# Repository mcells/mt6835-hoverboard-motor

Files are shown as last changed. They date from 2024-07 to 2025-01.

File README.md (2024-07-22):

# mt6835-hoverboard-motor
MT6835 Breakout board, eg. for mounting inside Hoverboard motors

| Front | Back |
| ----- | ---- |
| Top side | Top side |

## Features
- MT6835 Encoder
- 25x25mm diagonal M3 mounting holes that are removable by breakaway sections
- 14.2mm diameter, making it small enough to fit onto the 15mm shaft of Hoverboard motors
- M2 mounting holes, 10.6mm apart to facilitate mounting.
  - Nonconductive screws or spacers are necessary to prevent shorts!
  - Designed to be screwed into corresponding M2 holes drilled and tapped into the shaft, the cabling will go through the drilled-out center of the shaft.
  - A similar approach is described [here](https://community.simplefoc.com/t/a-project-in-mind-force-feedback-wheel/952/27)
- Breakaway drill template
  - drill out the motor shaft to 5mm and use the drill bit to locate the template on-center, then mark and drill the M2 holes
- All usable Pins broken out to three sensible 6-pin headers
  - SPI interface on 1.27mm header, with enough space to mount a 6-pin 1.25mm Molex Picoblade
  - UVW and ABZ (together with CAL and PWM pins) on 1mm Pitch headers (due to space constraints)
- TVS diode footprint can accept the one from the breakout board commonly available on Aliexpress
- Sleek design
## Renders
| Front | Back |
| ----- | ---- |
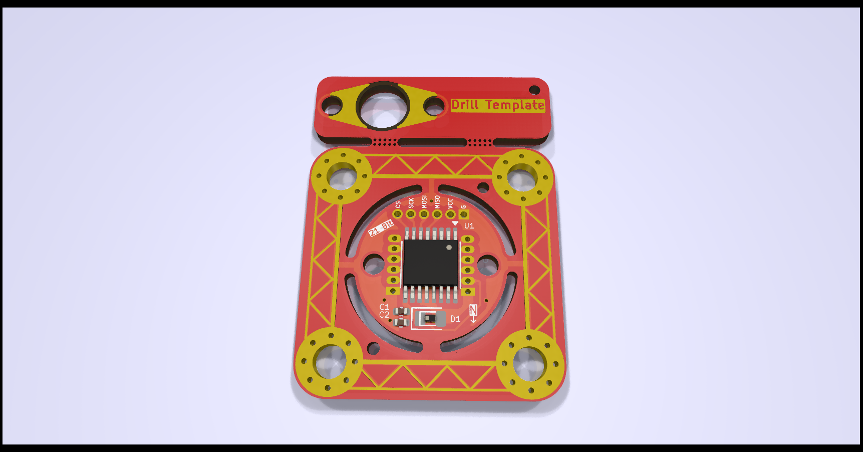
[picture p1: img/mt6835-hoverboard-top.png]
Top side
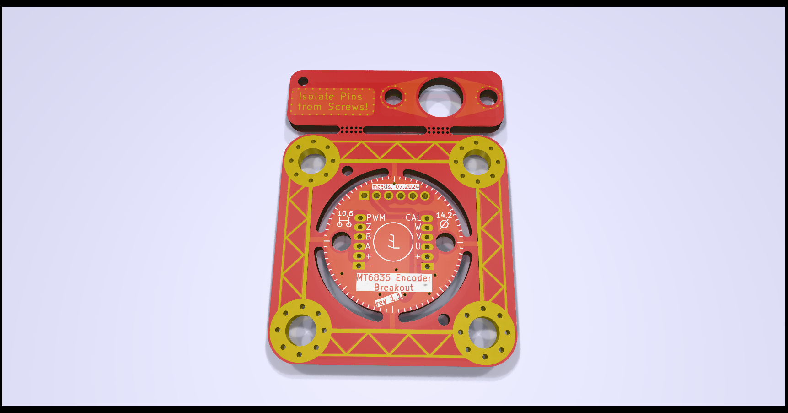
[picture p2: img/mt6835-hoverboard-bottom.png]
Bottom side
|  |  |

## Installation inside a Hoverboard motor

Installing the sensor board inside a Hoverboard motor requires you to have access to the following tools:
- A Hoverboard motor and
- A sensor board (obviously...)
- A drill press (though using a hand drill might work, if you are careful)
- 5mm HSS drill
- 2mm HSS drill for marking the locating holes
- 1,6mm or 1,7mm HSS drill for the M2 threads
- M2 tap
- two M2 screws for mounting the sensor
- soldering stuff
- a saw or dremel to cut out the round part of the PCB

### Steps

| Step | Image | Description |
| ---- | ----- | --- |
| 1  | | Disassemble the Motor, until you have just the bare Stator. Desolder and pull out all wires, so you can drill through the shaft.|
| 2  | Step 2 | Drill a 5mm Hole inside the top of the stator shaft. There is a centered "dimple" already in the shaft, which helps with centering the drill enormously. You want everything to be as concentric as possible, else you will get a periodic nonlinearity in the measured angle! You have to drill about 25mm until you break through to the hollow shaft. |
| 3  | Step 3 | Remove the drill bit from the drill and put it most of the way through the new hole, so that just protrudes at the top. Use the drill bit to locate the template PCB on the center of the shaft. | 
| 4  | Step 4 | Either use a center punch, or, using a M2 drill bit, pre drill two "dimples", so you can later locate with the smaller drill bit. When drilling the second dimple, use something like a small allen wrench in the first dimple to hold the template in place. |
| 5  | Step 5 | Drill the two holes with a 1.6mm or 1.7mm bit and tap the holes to M2. You can use a 1.7mm drill to ease the tapping, as the threads don´t need to support any significant load. Also refrain from tapping more than a few mm deep, as it is absolutely not neccesary and just increases the risk of your tap snapping off. |
| 6  | Step 6 | You can now mount the sensor. Take care to use either 3d printed isolators like I did, or use plastic washers. Else you **will short** the sensor out! I had to drill out the 5mm hole to 6mm to make my sensor wires fit. If you have thinner wires, 5mm might be enough for you. I replaced the original wiring with new one. |
|  7 (optional) | Step 7 | In these motors, the 3 phases are each wound using multiple strands of enamelled copper wire, some 3, 4, or even 5 in parallel. The phases are then connected in a star, or Y topology. I wanted to lower the kV as much as possible, so I unsoldered the strands and connected them in series for each of the three phases. This lowers the kV by the number of strands you serialize, in my case three. |
|  8 | Step 8  |  My motors have just enough space inside, so that the magnet can be mounted directly inside the rotor bell. I marked the center of the bell by pushing a 15mm HSS drill into the bearing (15mm inside diameter) and turning the bell. This leaves a perfectly centered dimple exactly where you want to mount the magnet. The aluminium there is about 2-3mm thick. Drilling about 1mm with a drill bit of the same diameter as your magnet lets you just glue the magnet there, without drilling from the outside. |

## Where to get the boards

I got my PCBs fabbed and assembled at JLC. You can use the provided KiCad project files to generate the required files.
You don´t have to get assembled boards directly, as I designed the PCBs so that you can desolder the components from the aliexpress board and solder them onto this PCB. This might be far cheaper for single quantities.

If you have any questions, feel free to just create an issue/discussion or ask me on Discord (@hollowedbethyname)

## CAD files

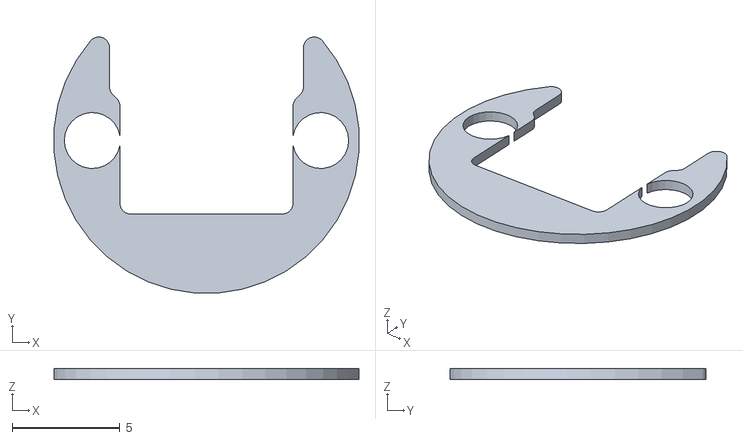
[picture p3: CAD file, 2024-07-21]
3d-prints/Isolator-top.stl
14.2 x 11.9 x 0.5

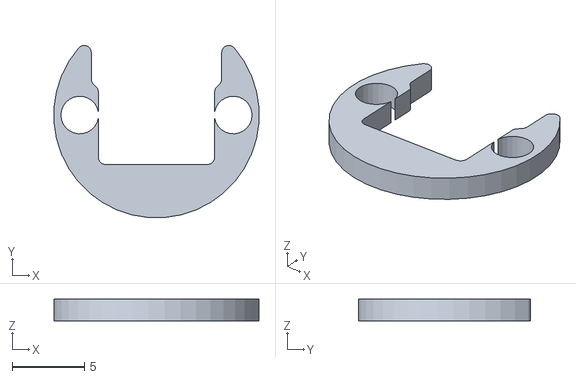
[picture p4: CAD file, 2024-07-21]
3d-prints/isolator-bottom.stl
14.2 x 11.9 x 1.50

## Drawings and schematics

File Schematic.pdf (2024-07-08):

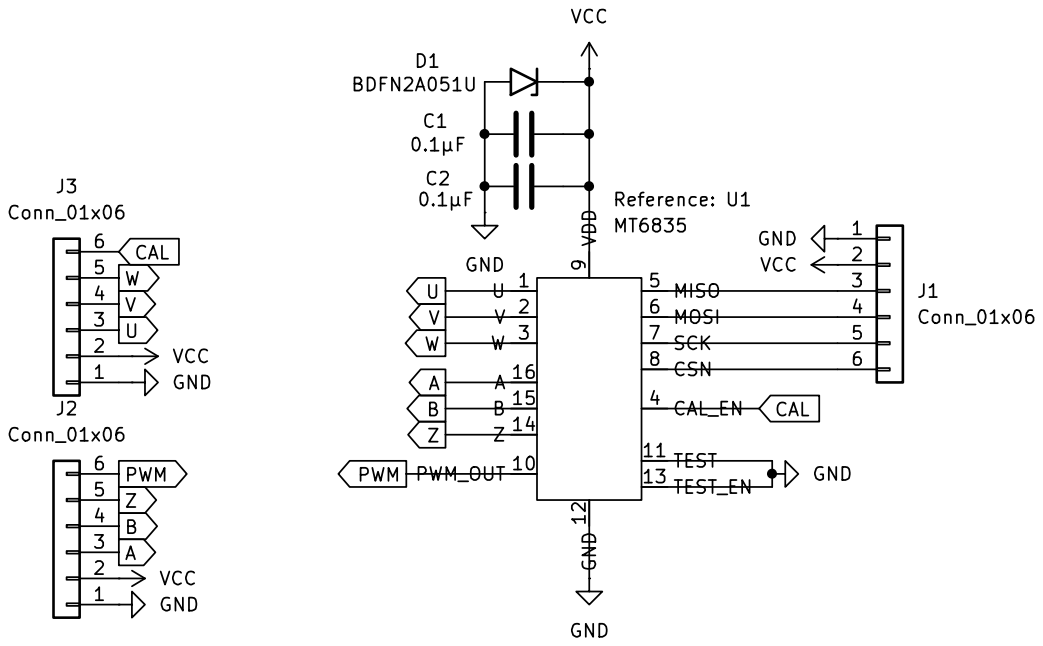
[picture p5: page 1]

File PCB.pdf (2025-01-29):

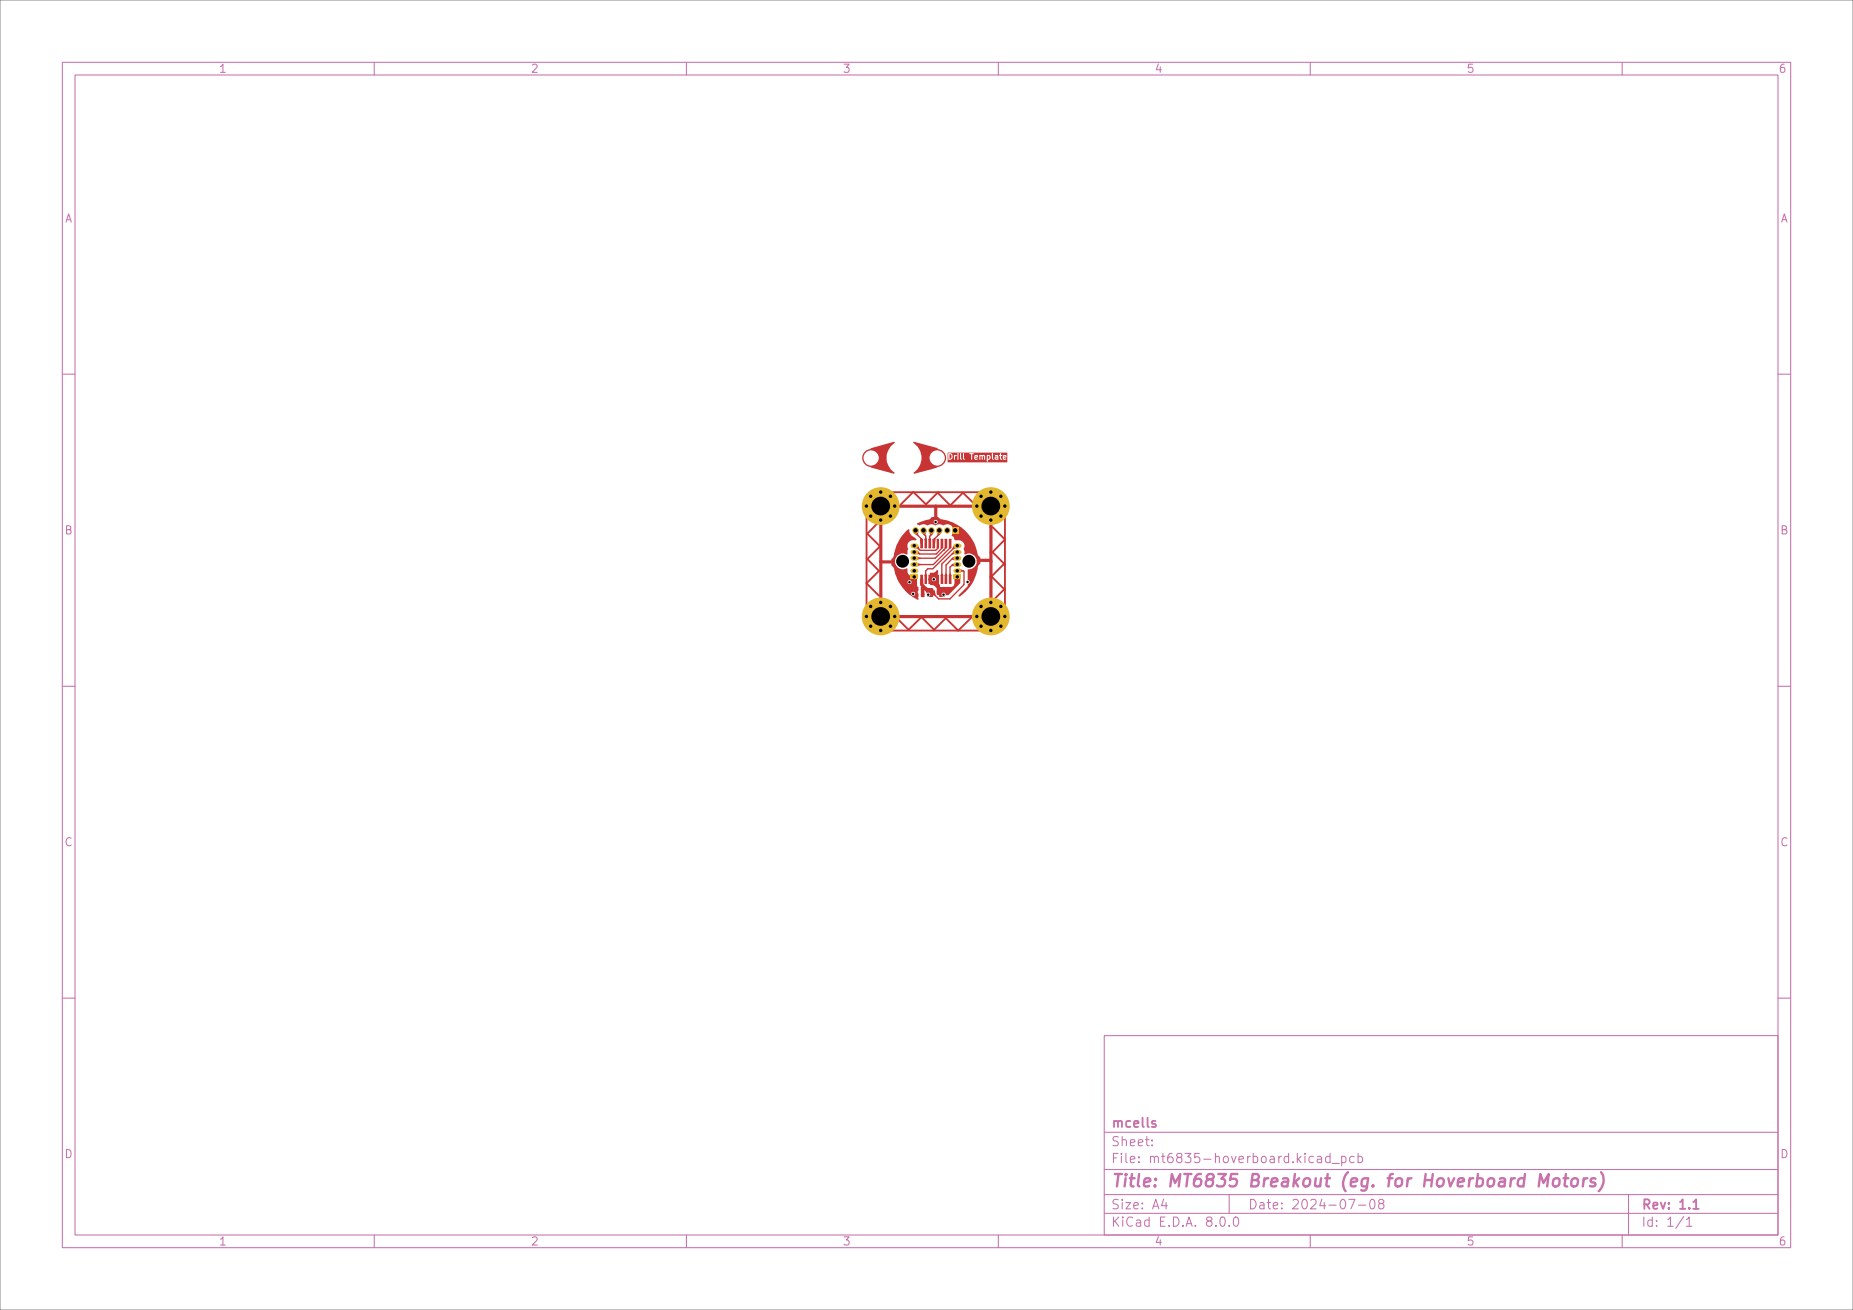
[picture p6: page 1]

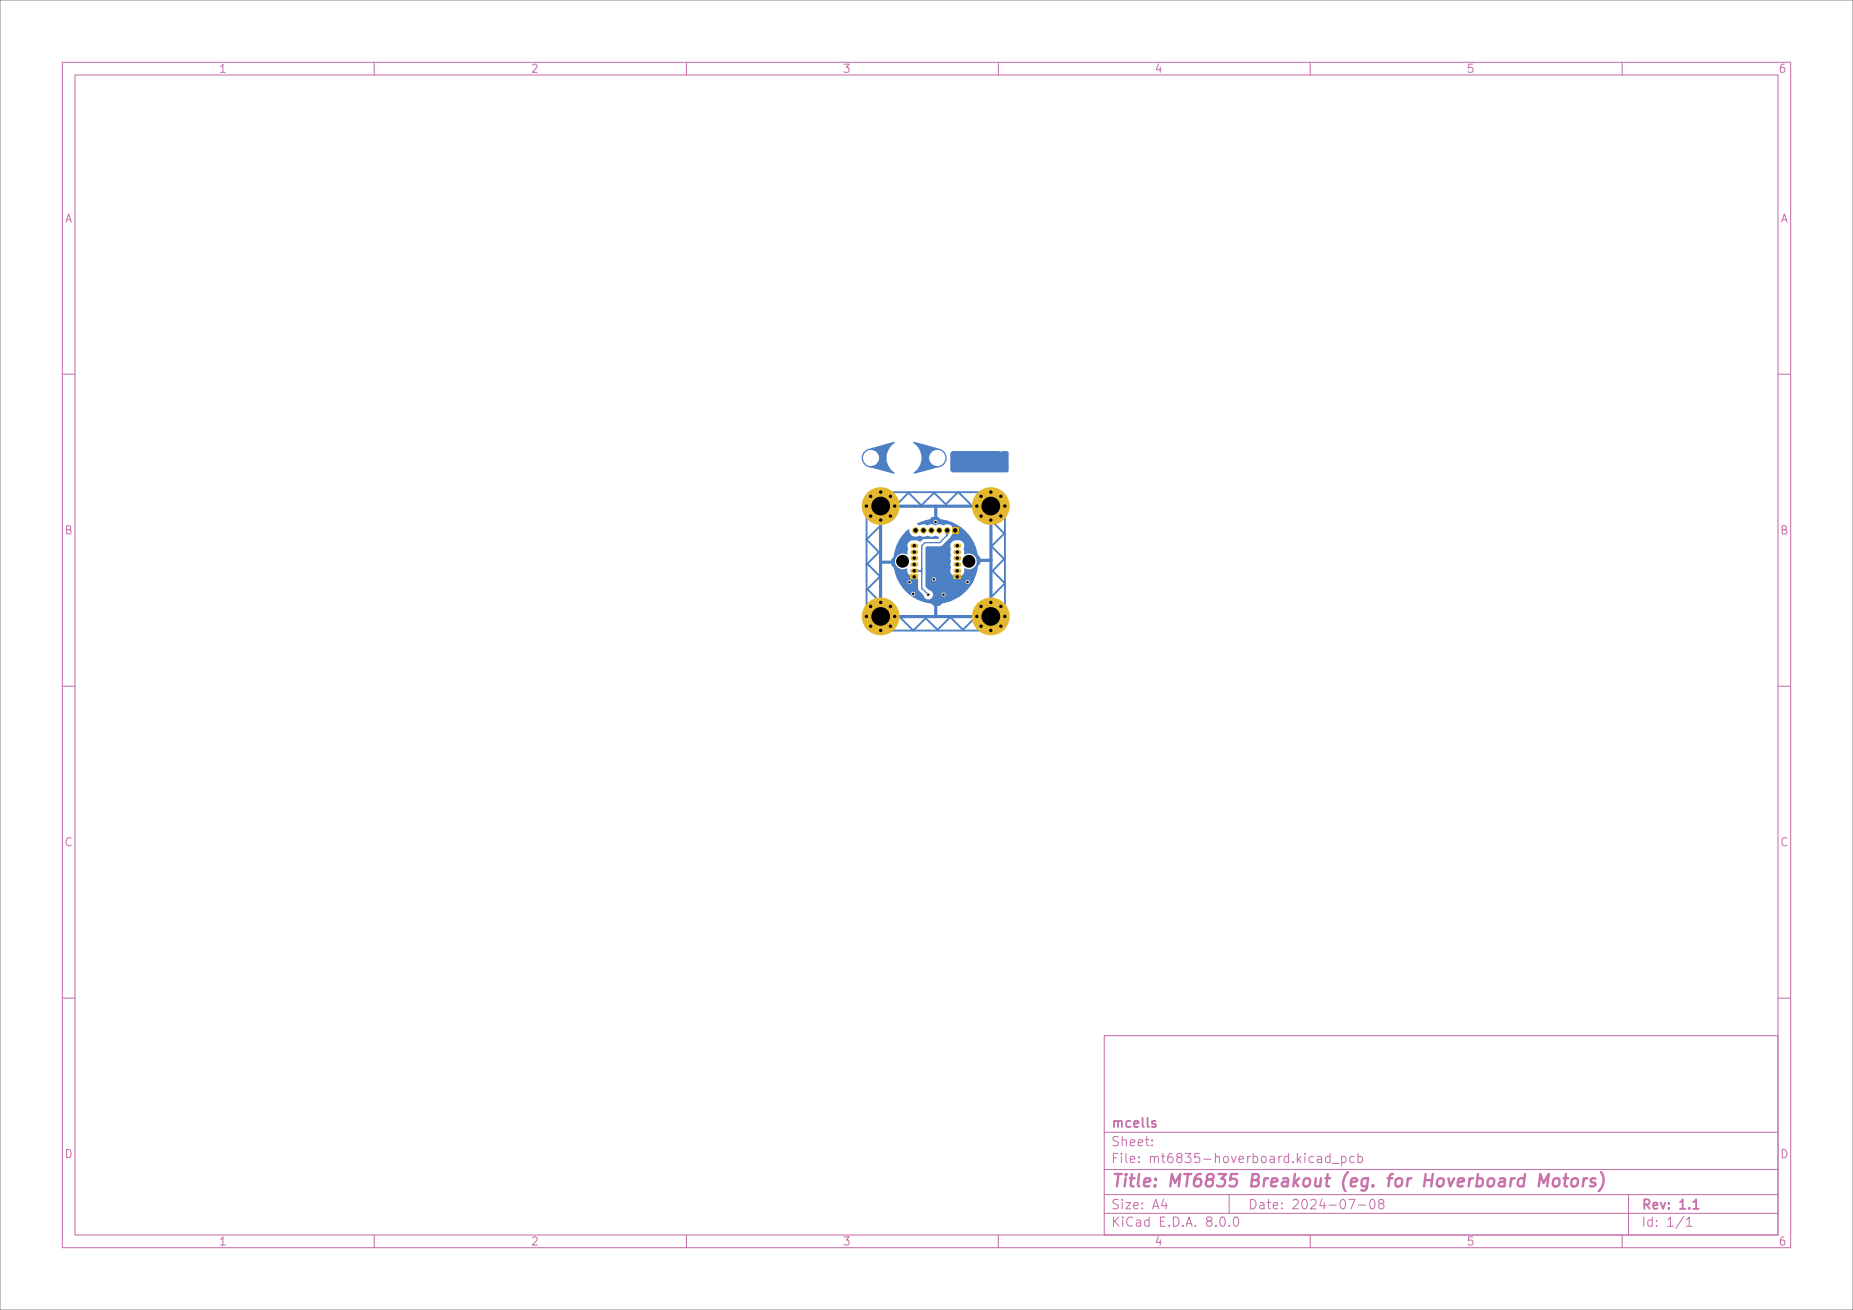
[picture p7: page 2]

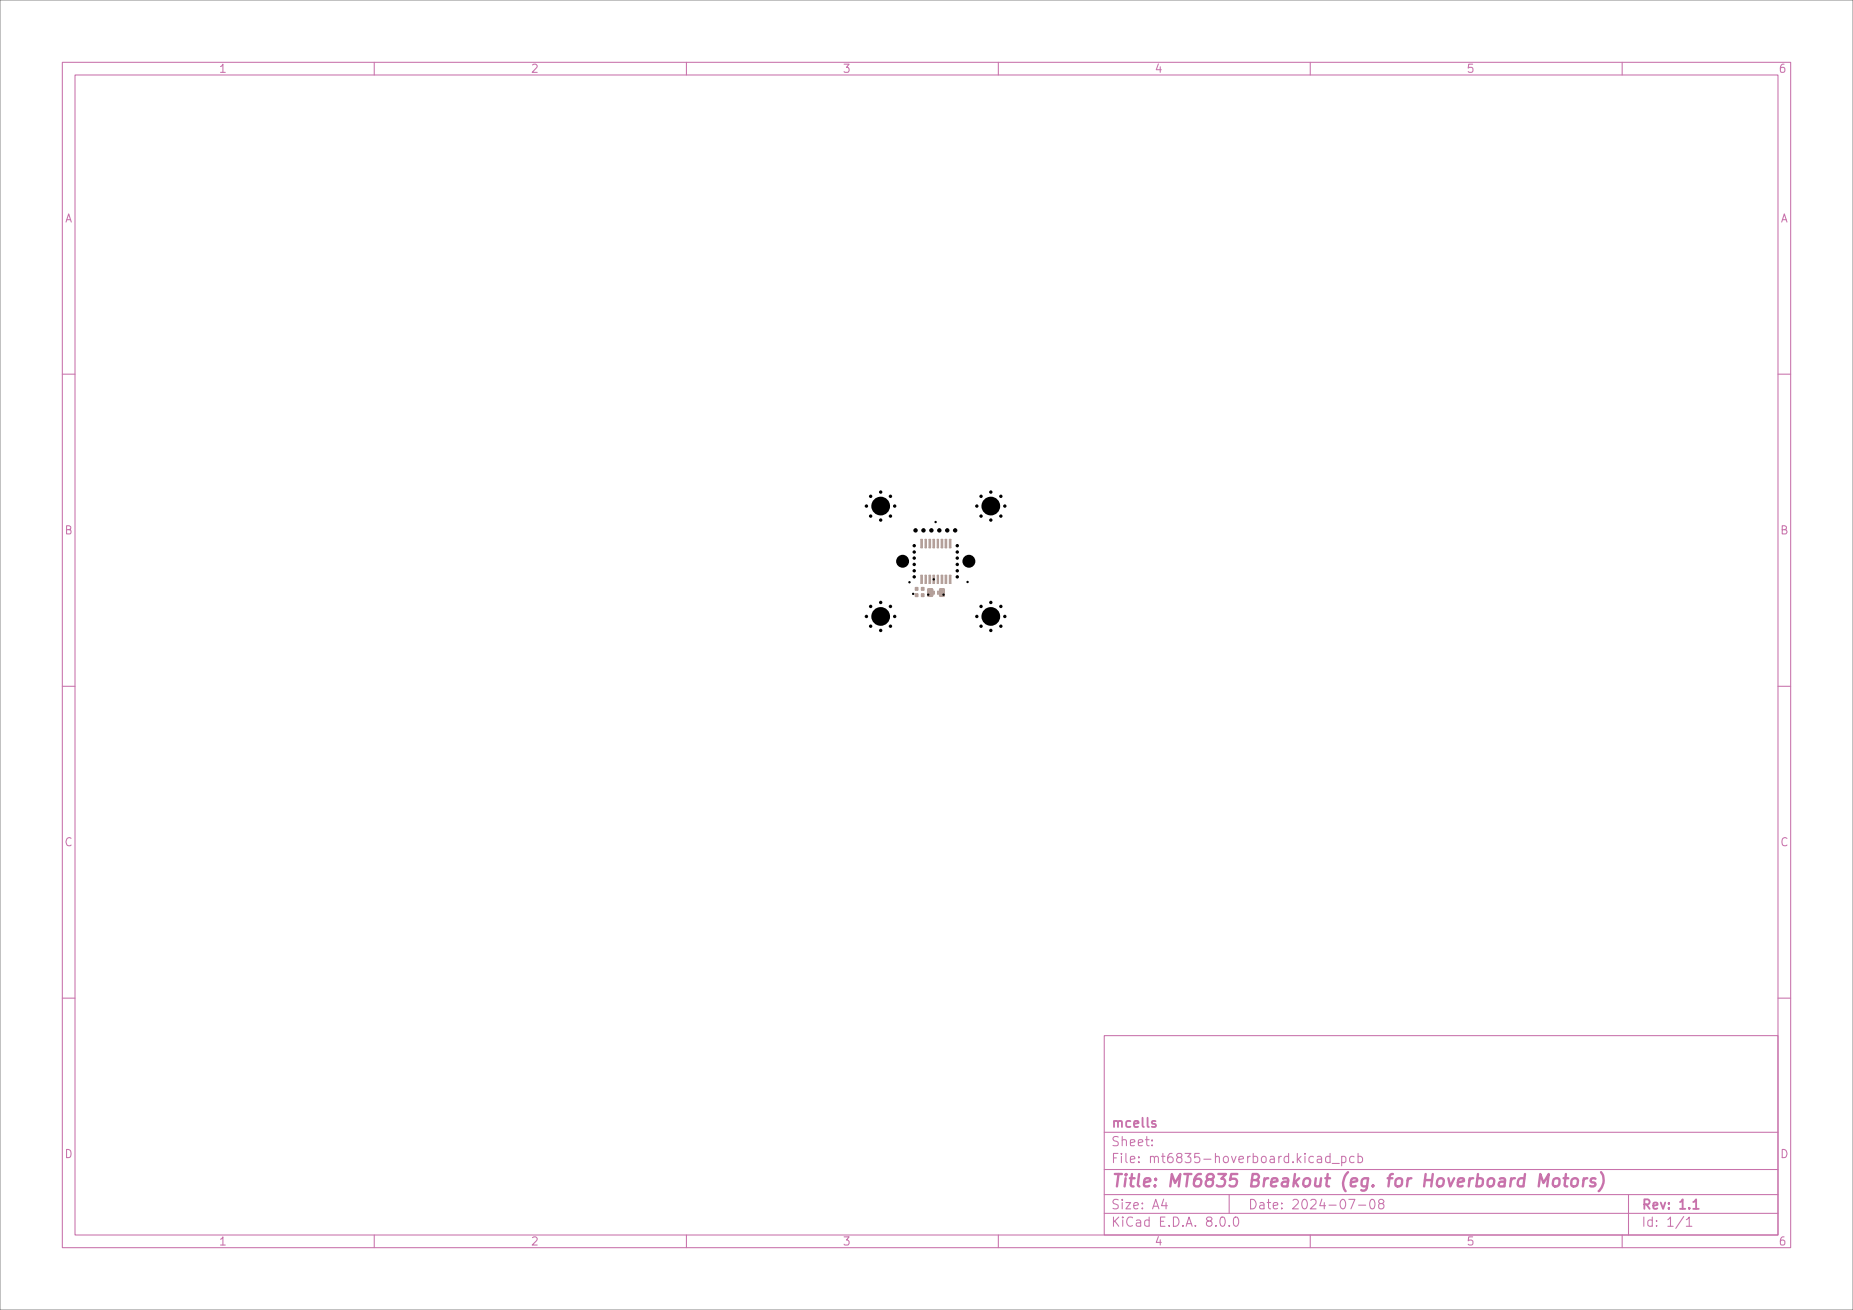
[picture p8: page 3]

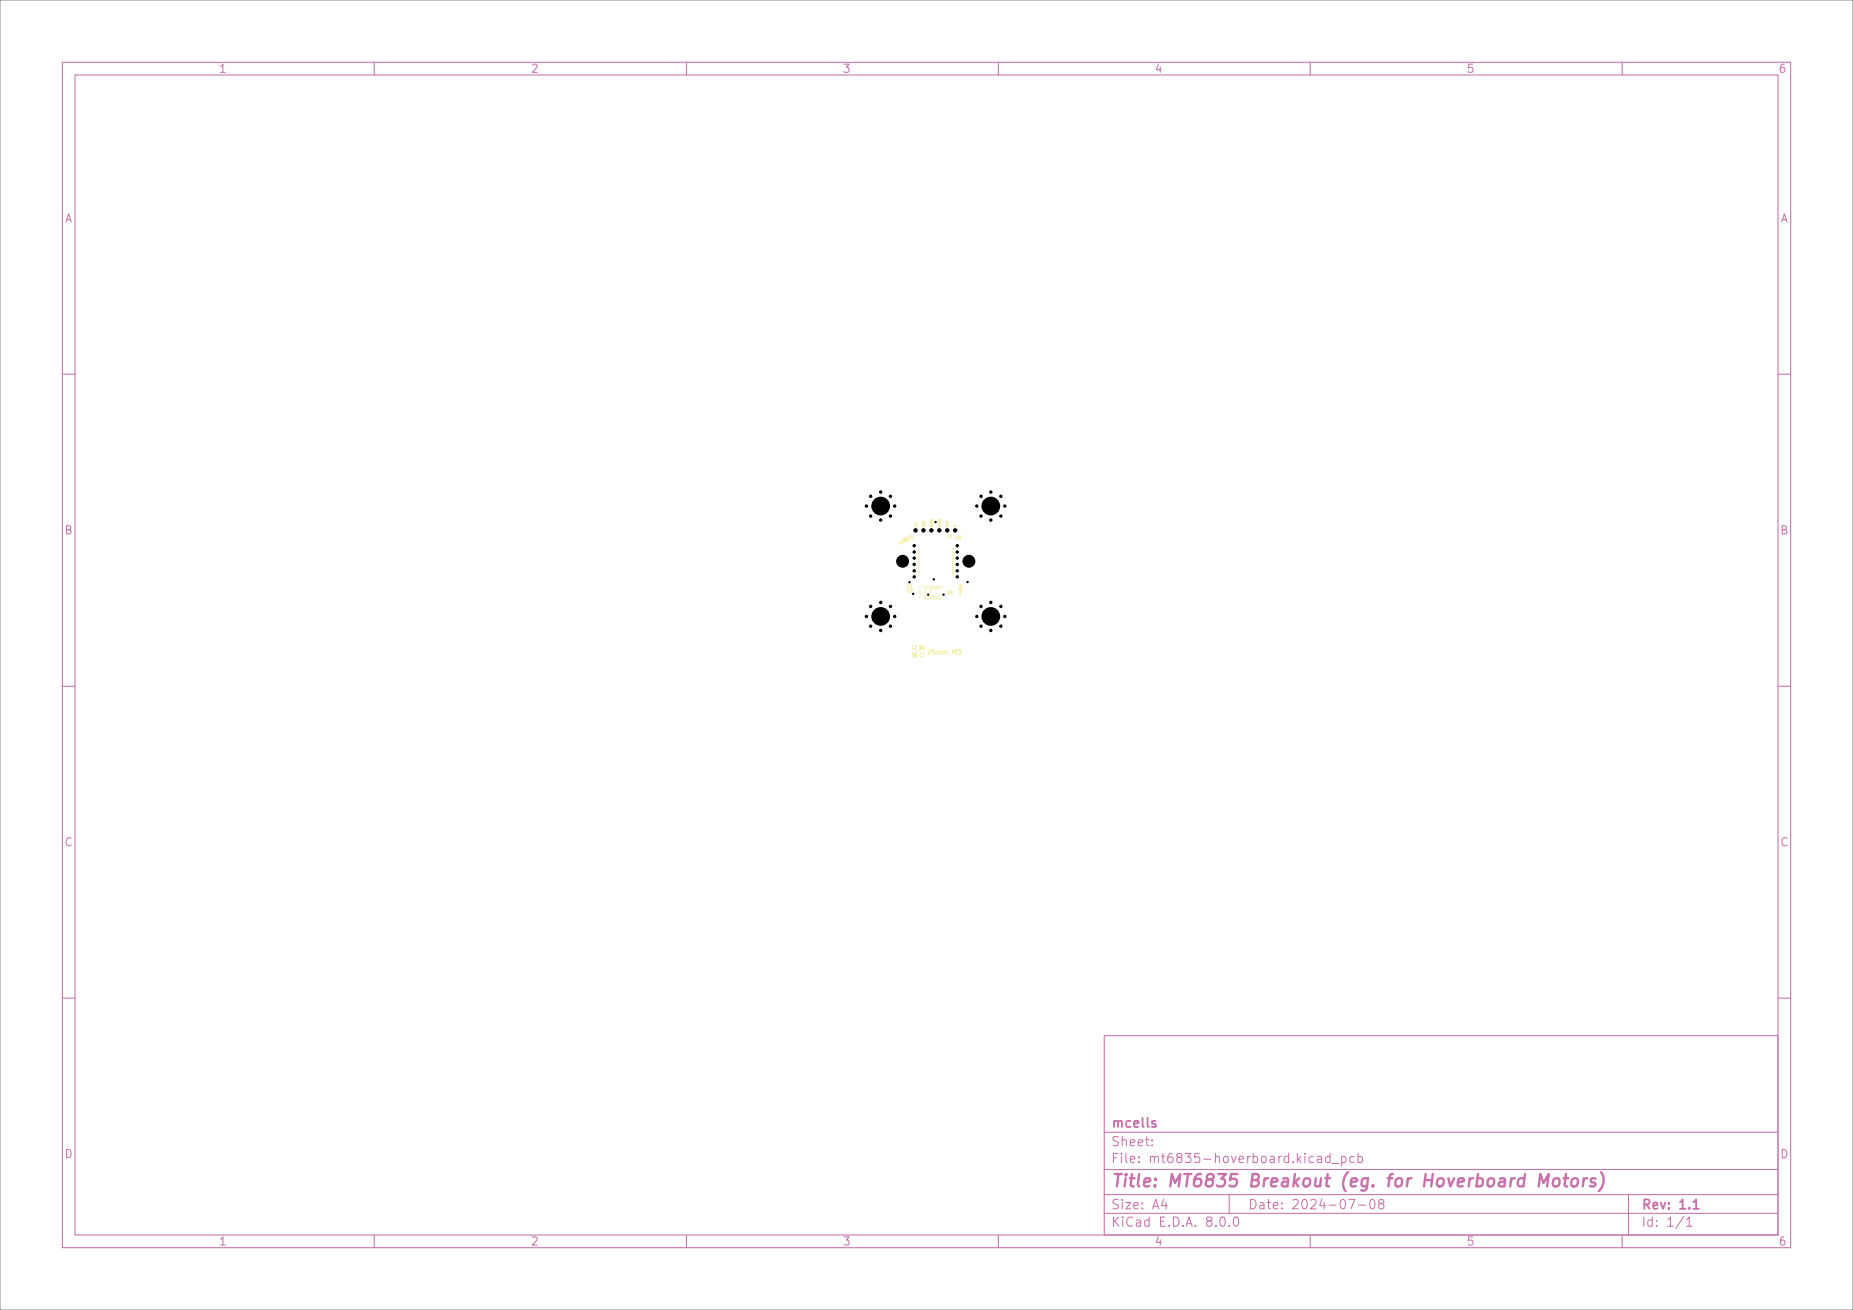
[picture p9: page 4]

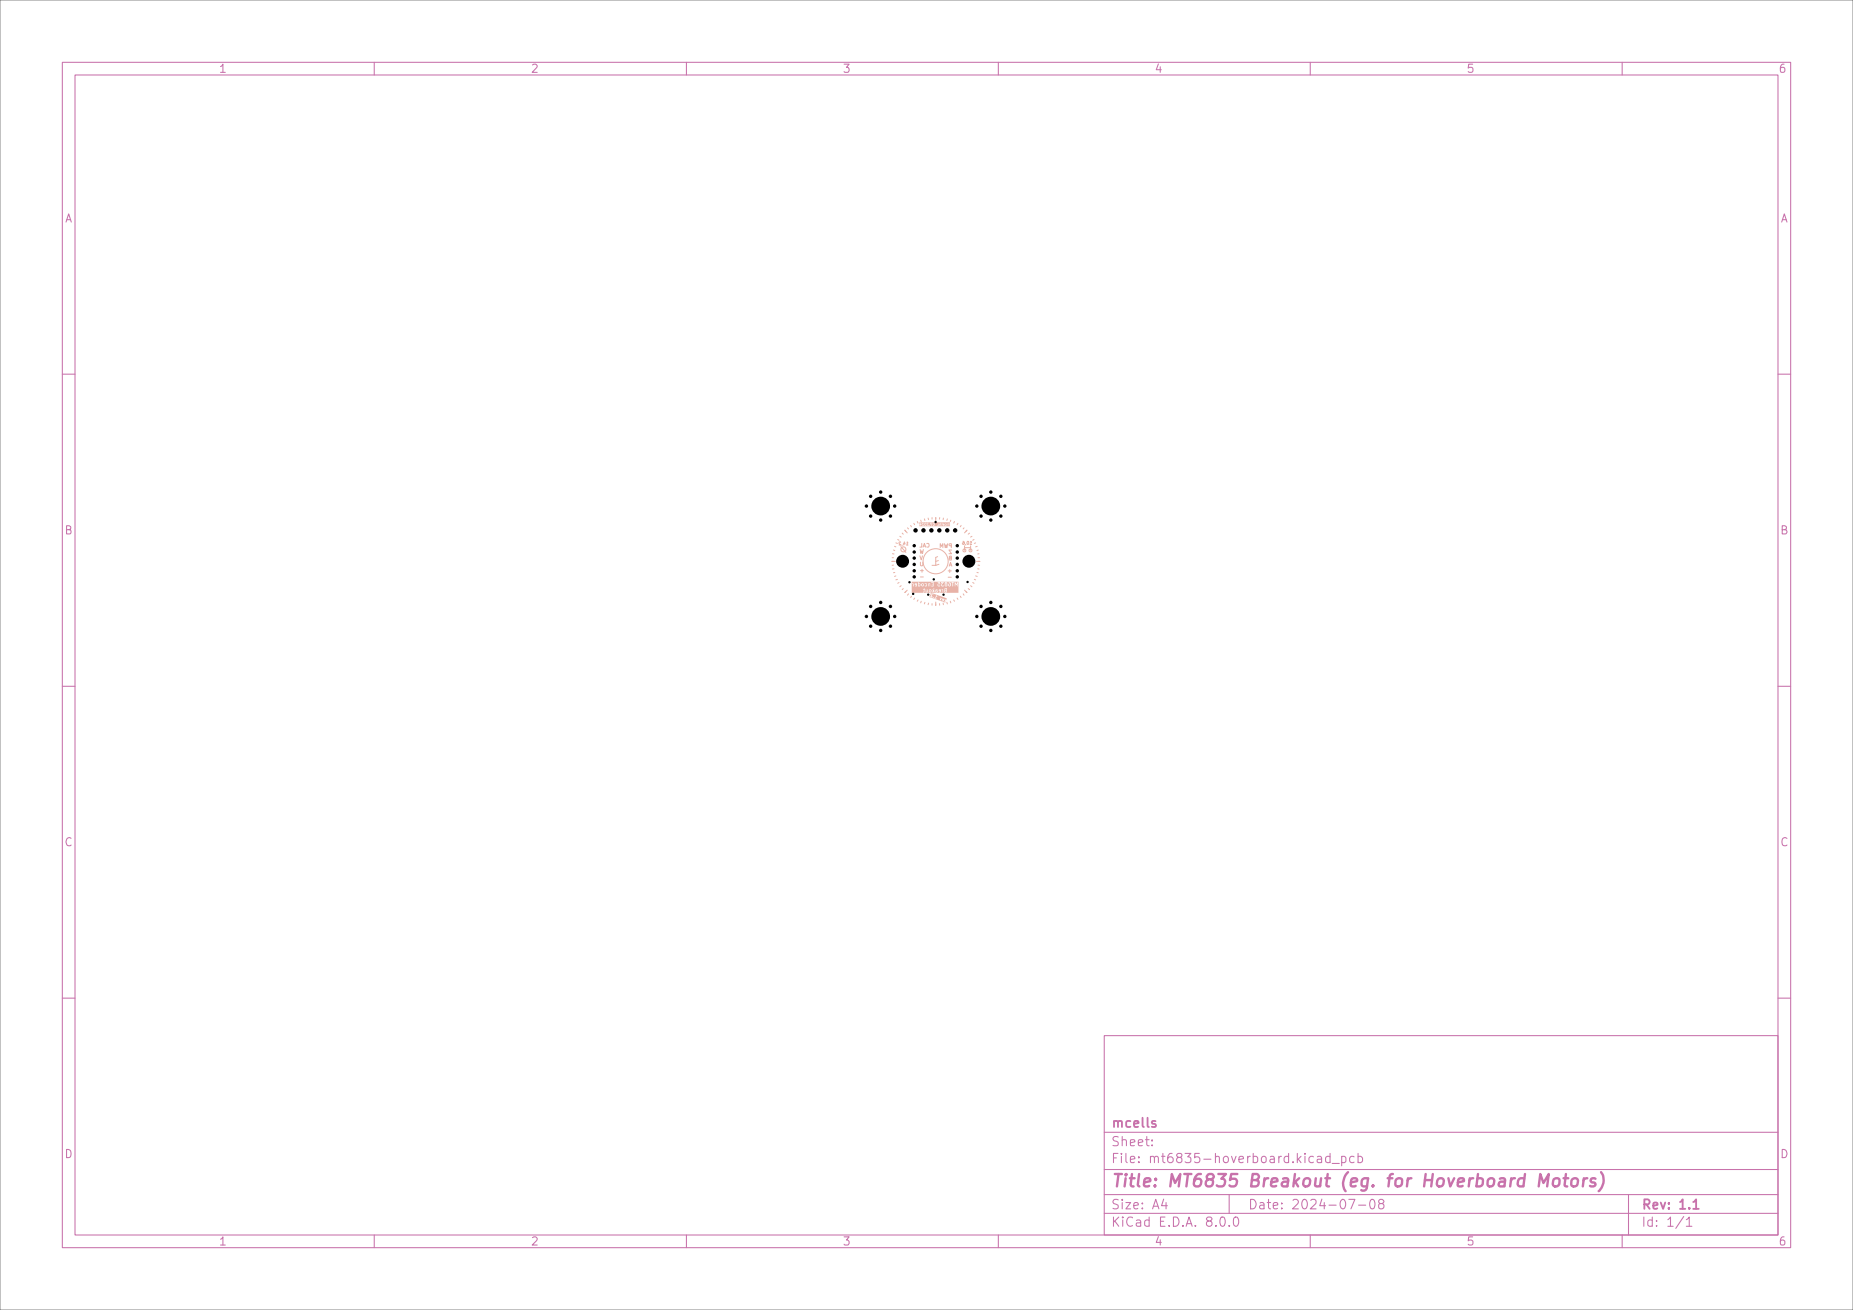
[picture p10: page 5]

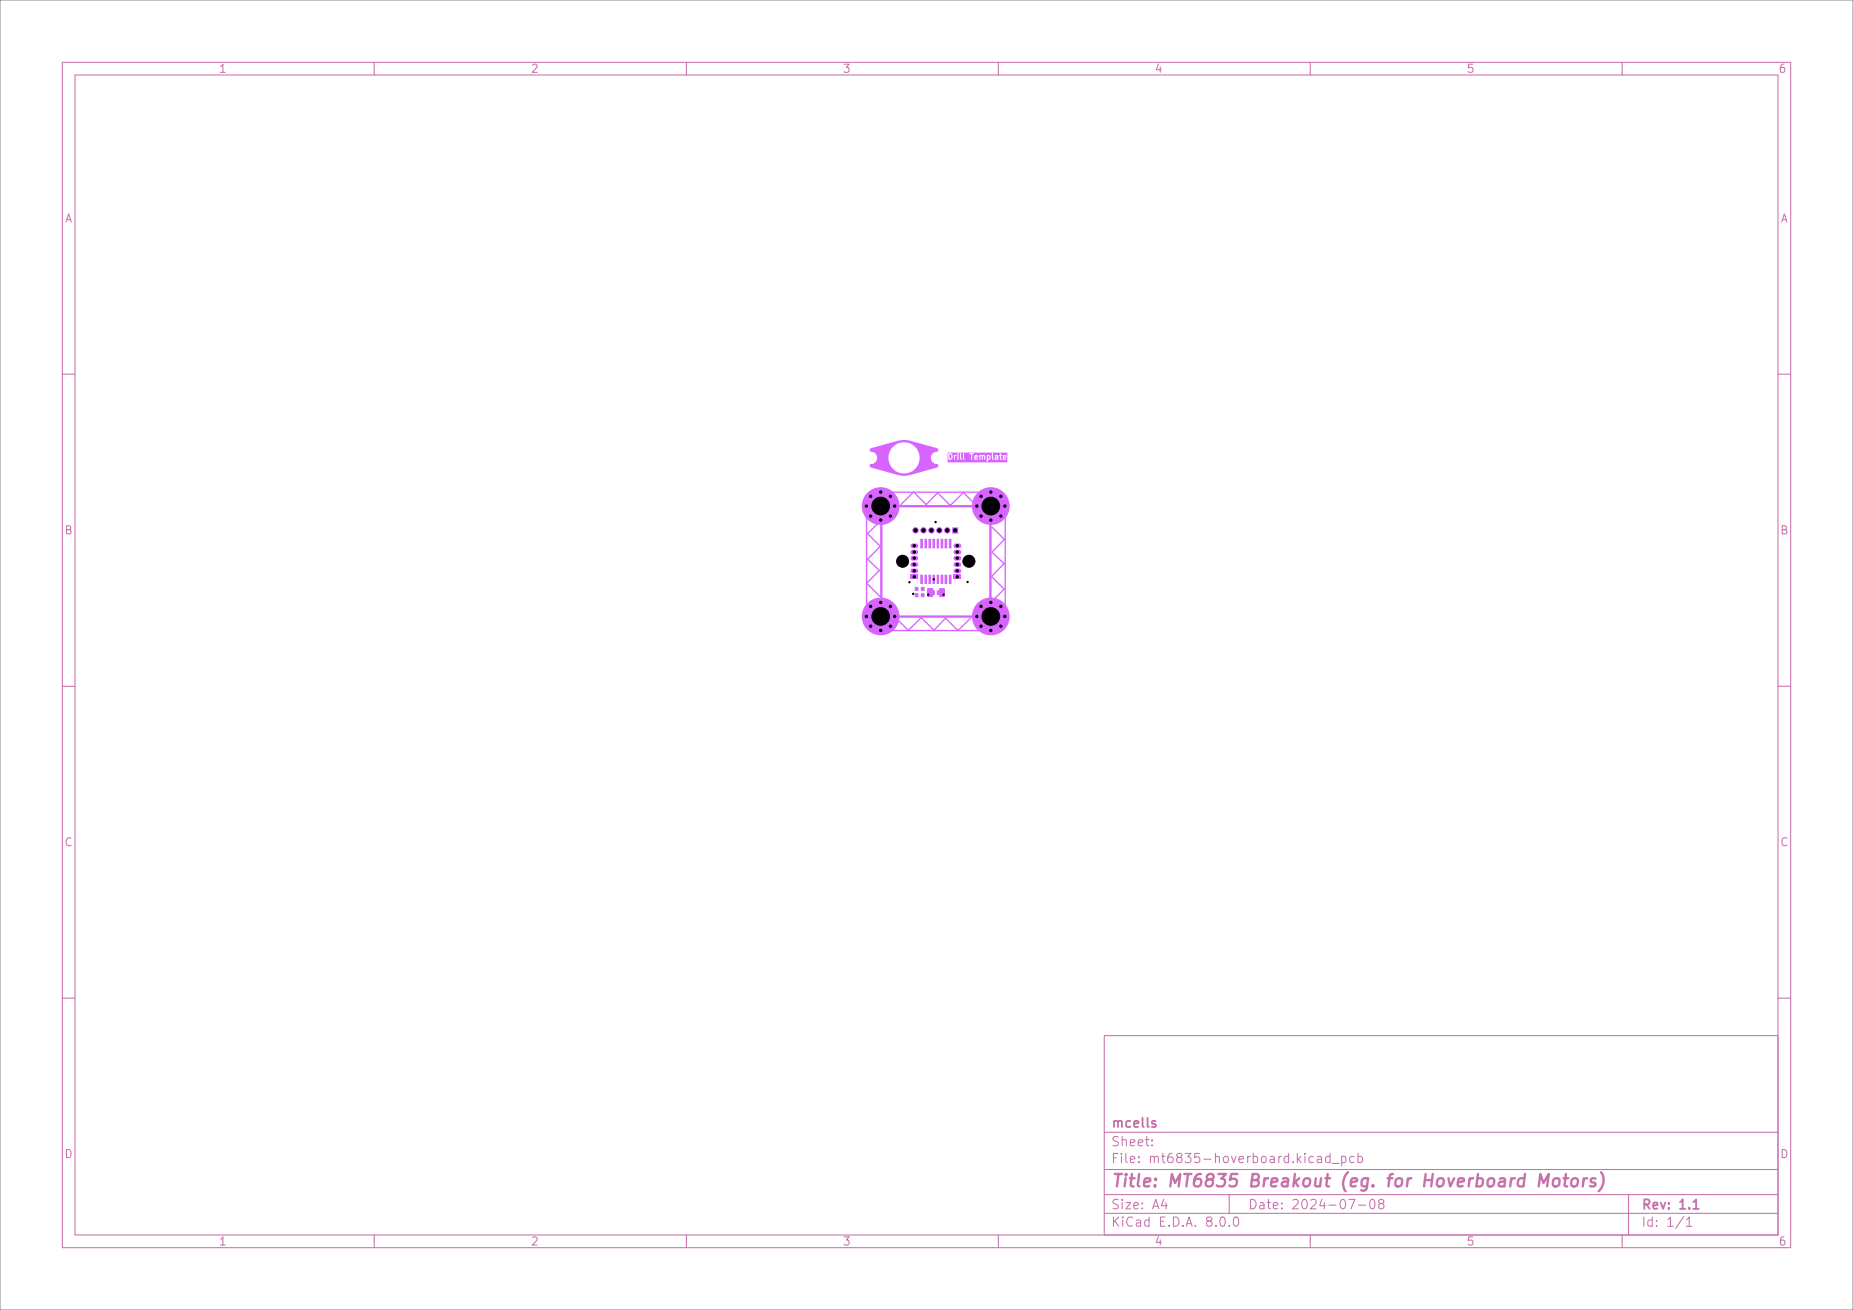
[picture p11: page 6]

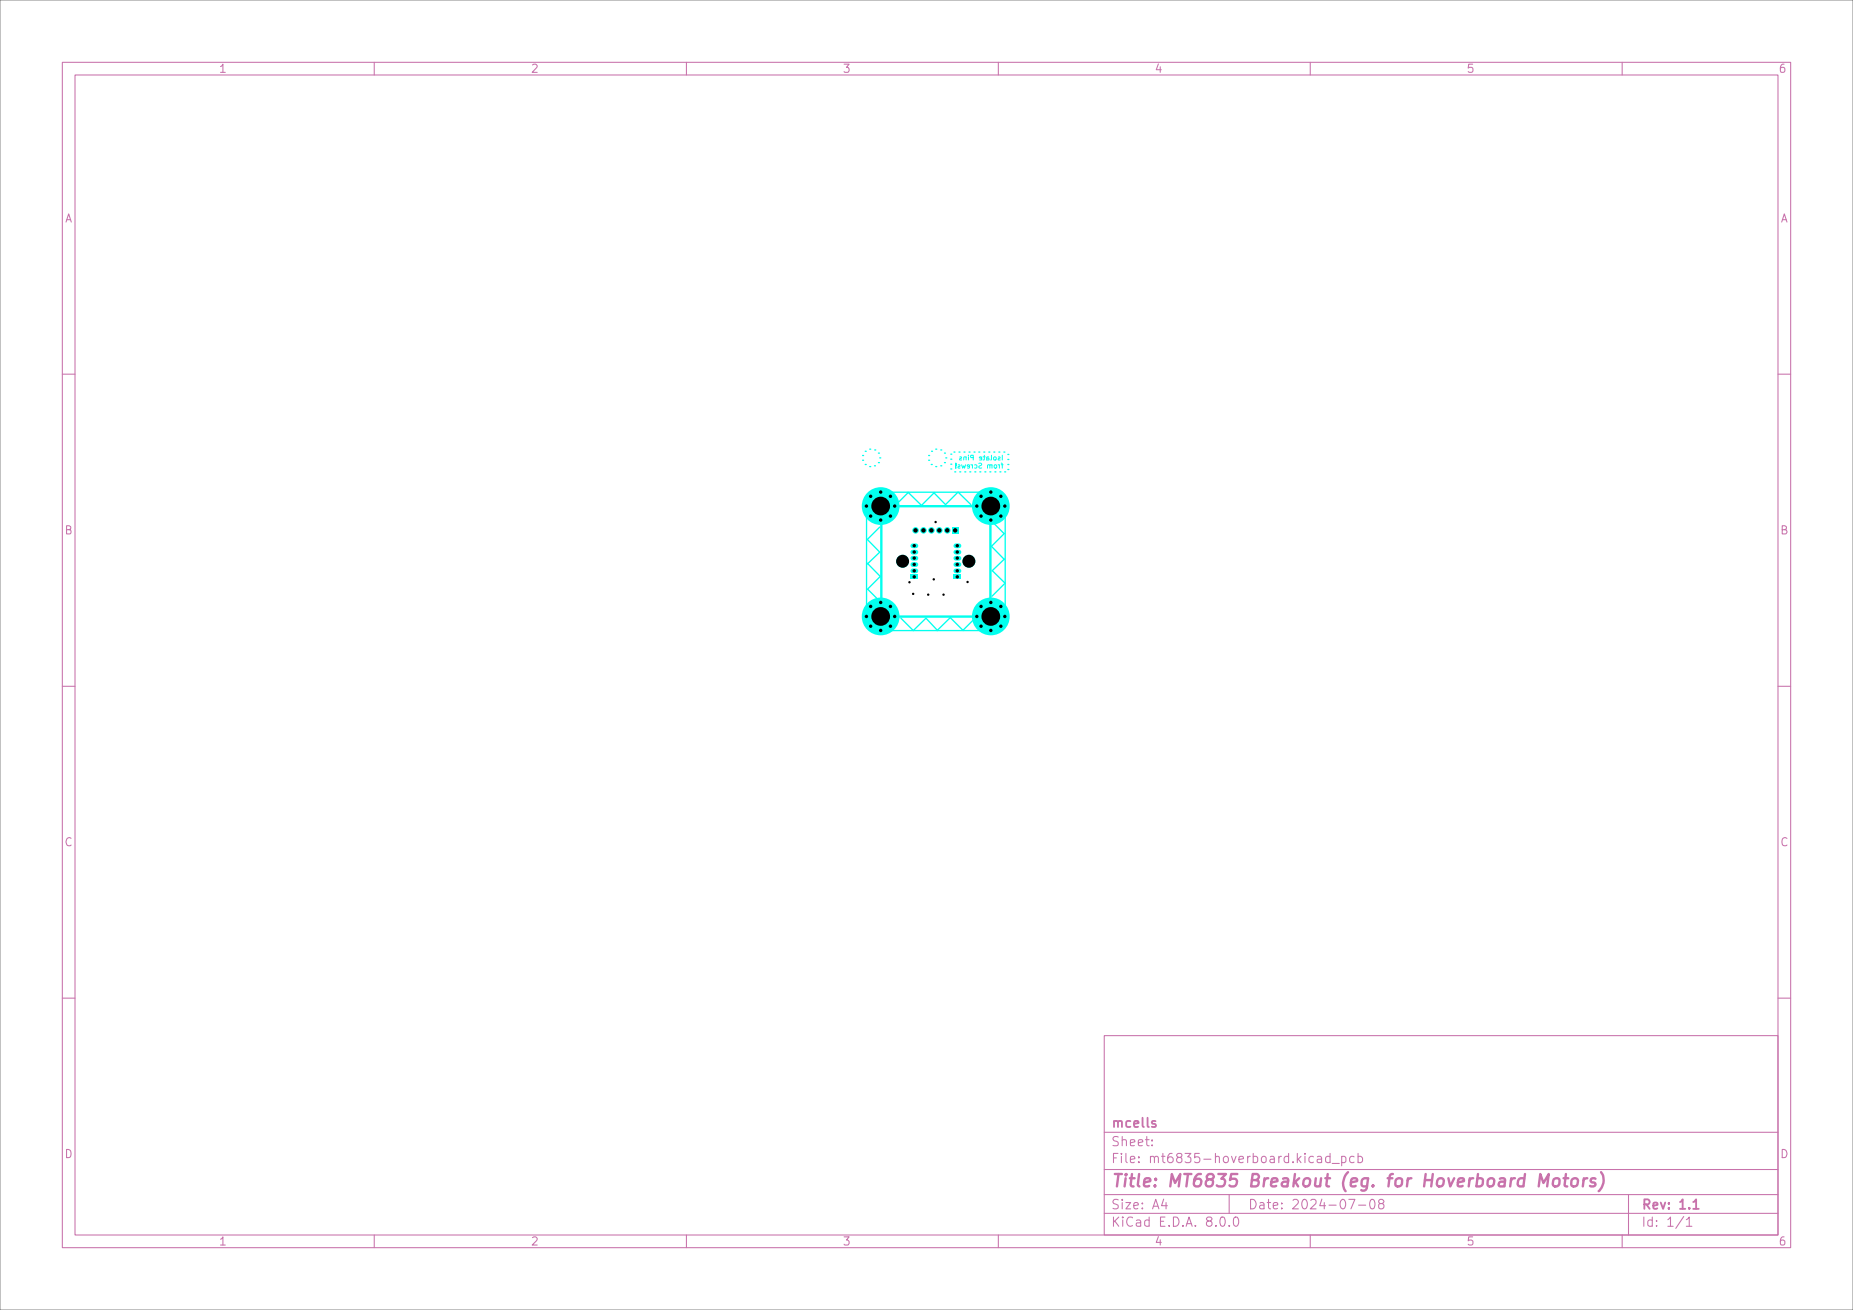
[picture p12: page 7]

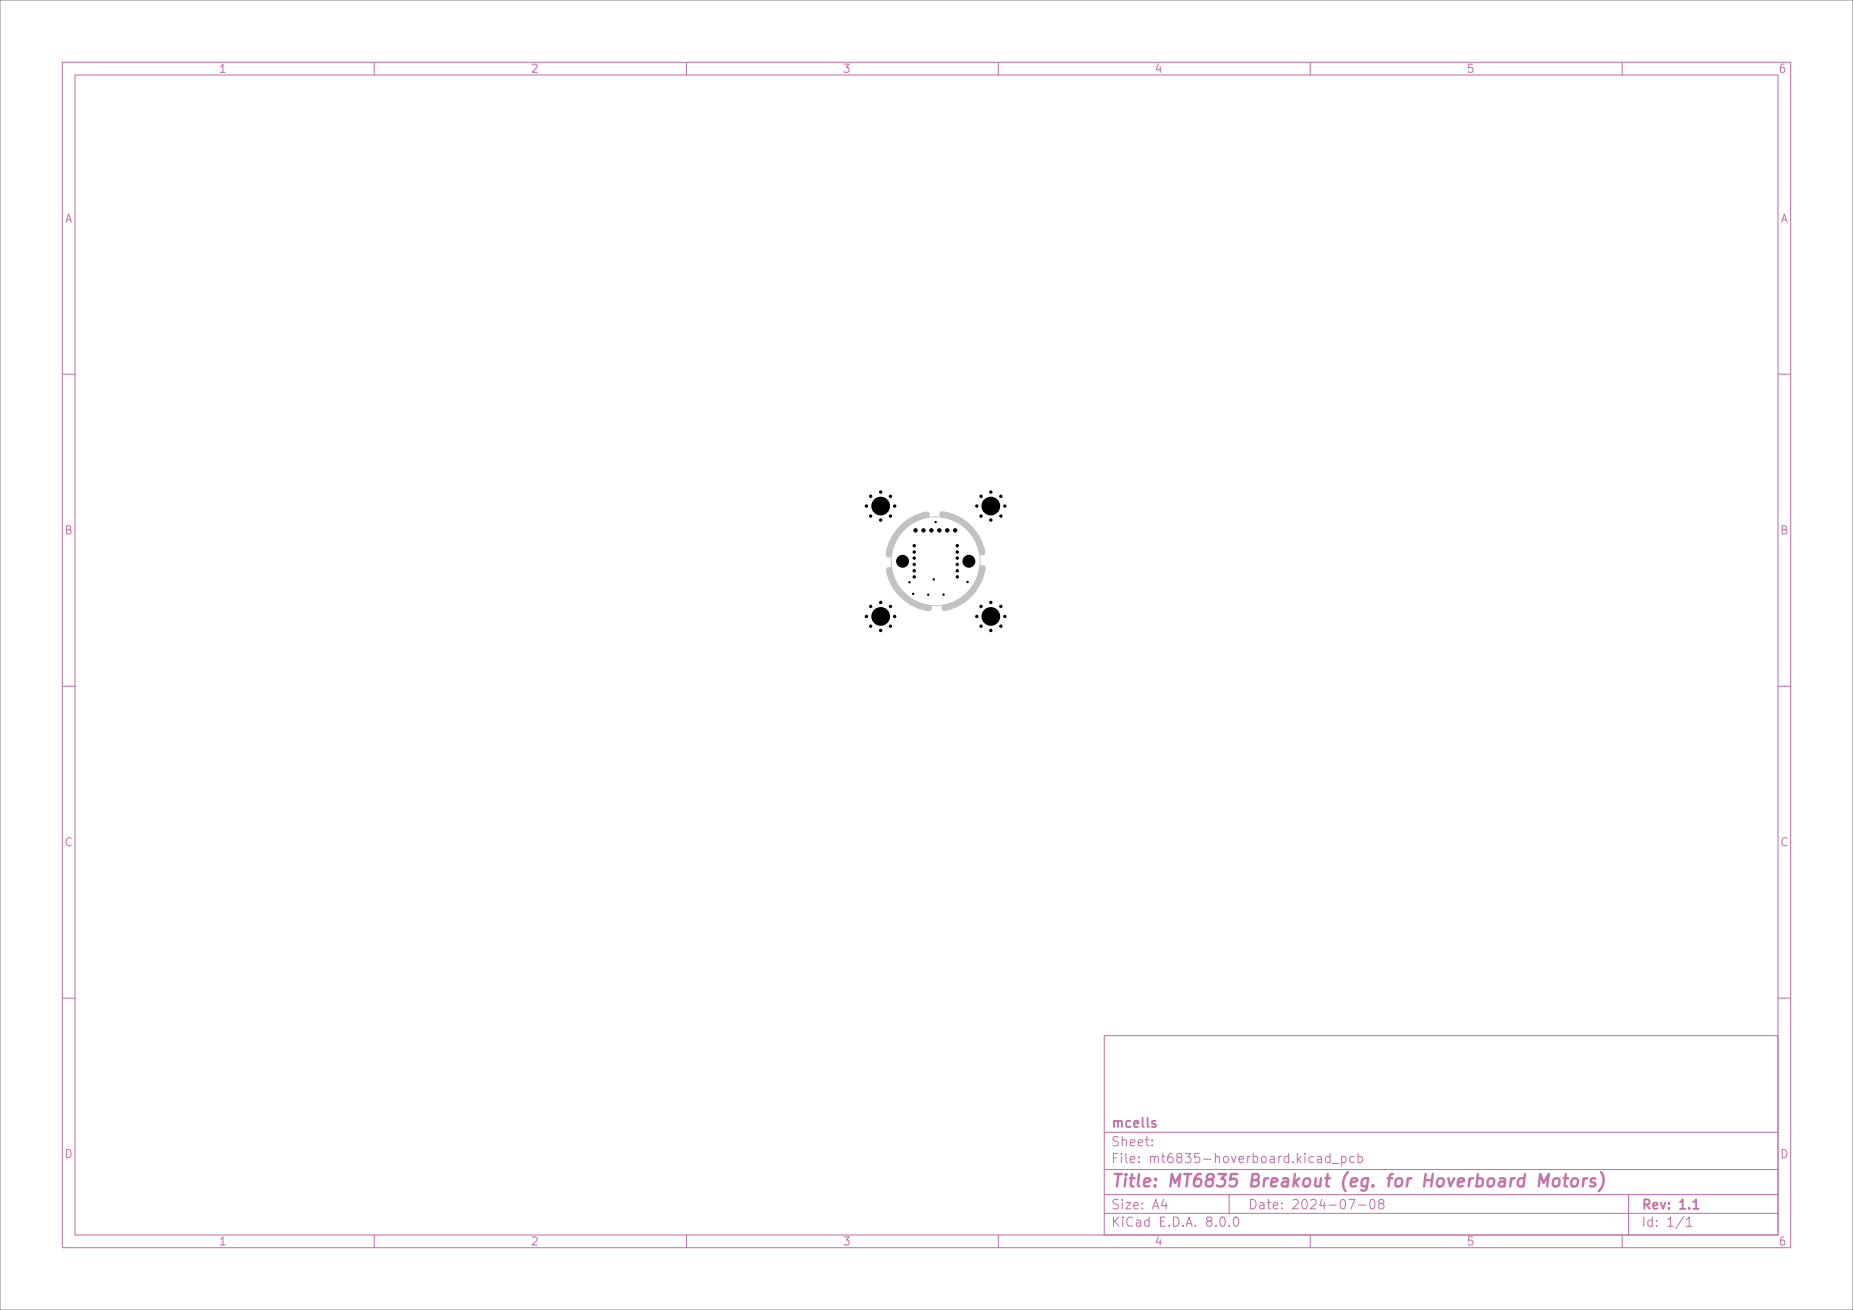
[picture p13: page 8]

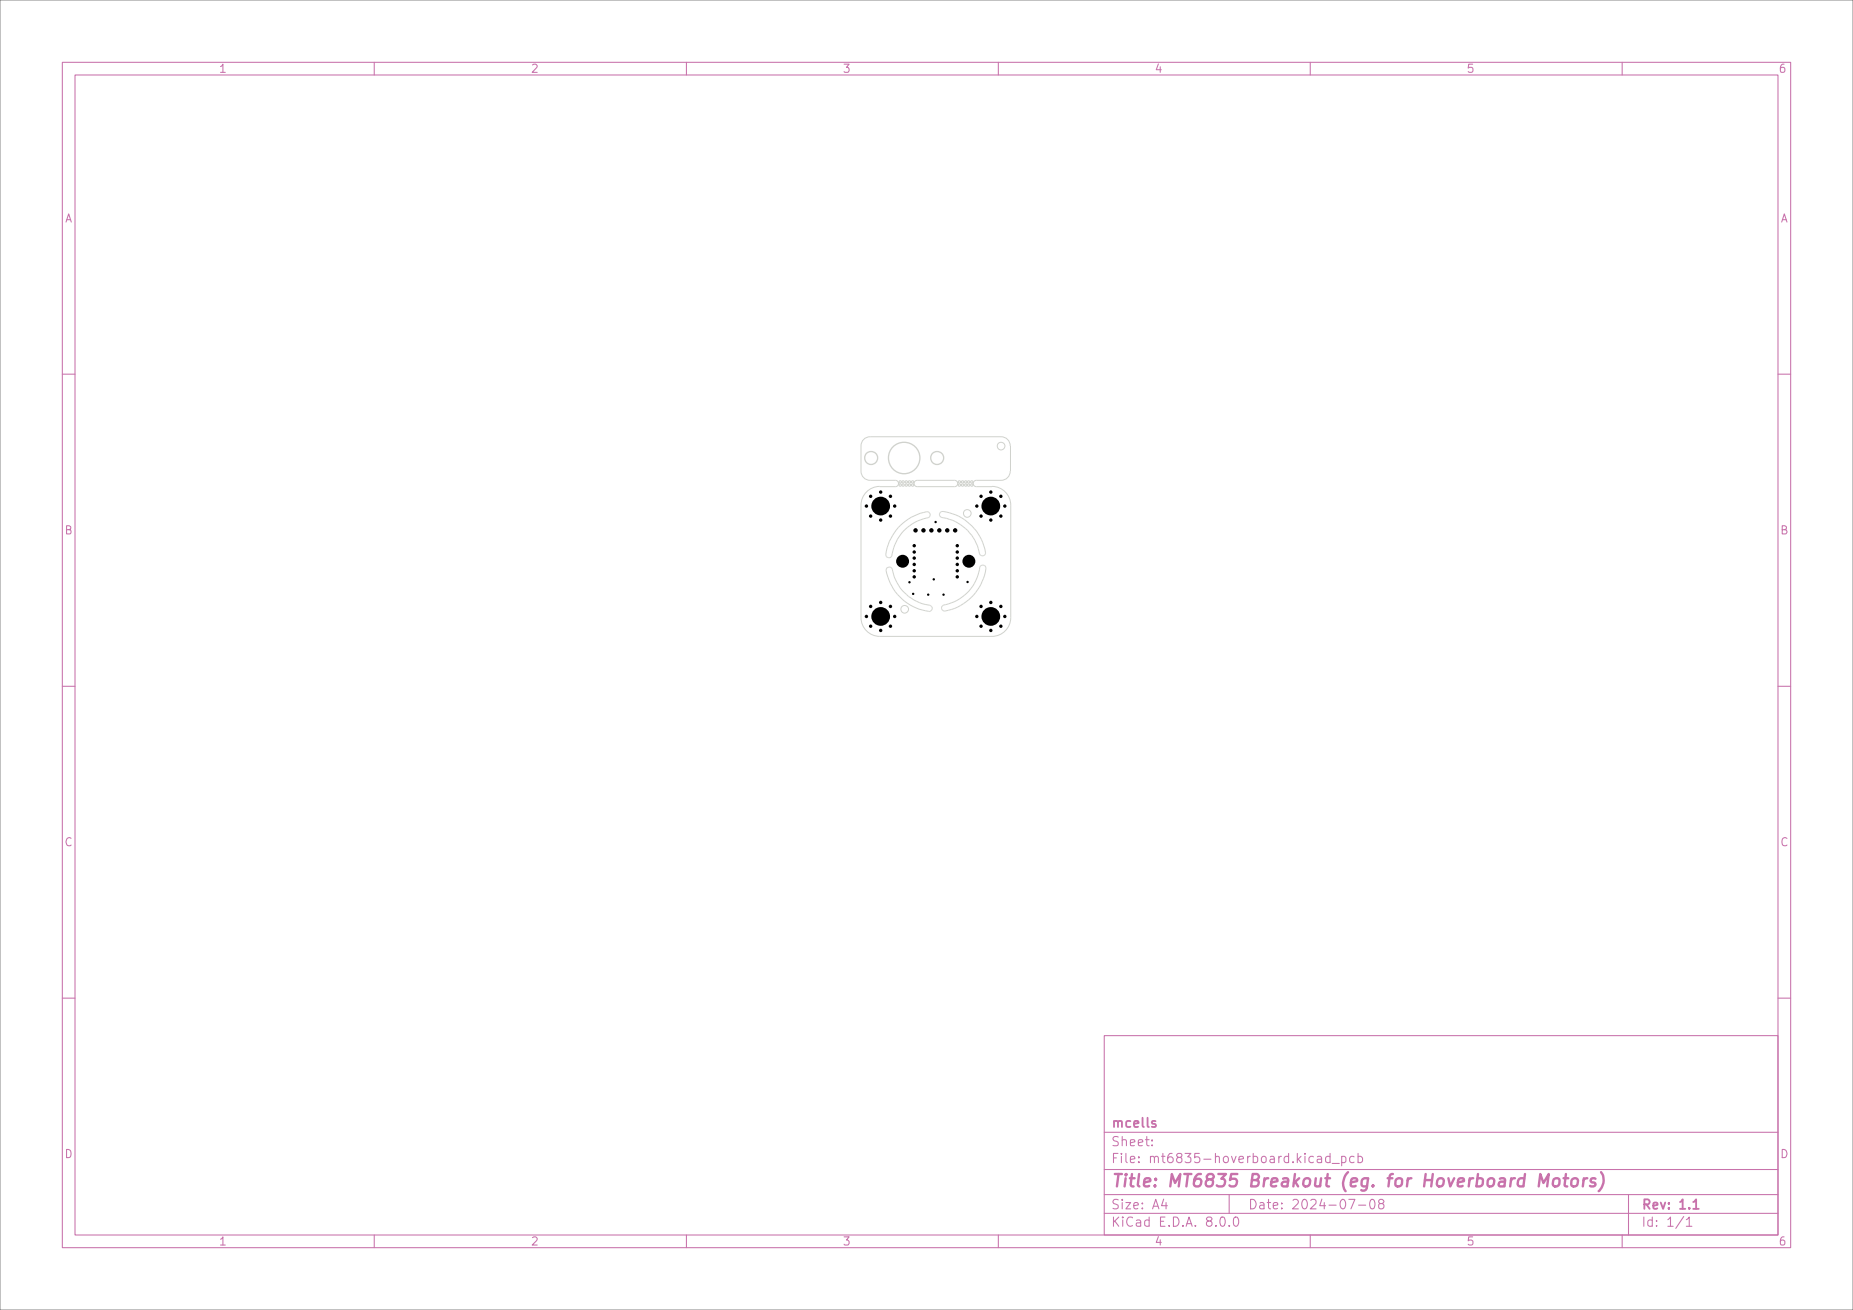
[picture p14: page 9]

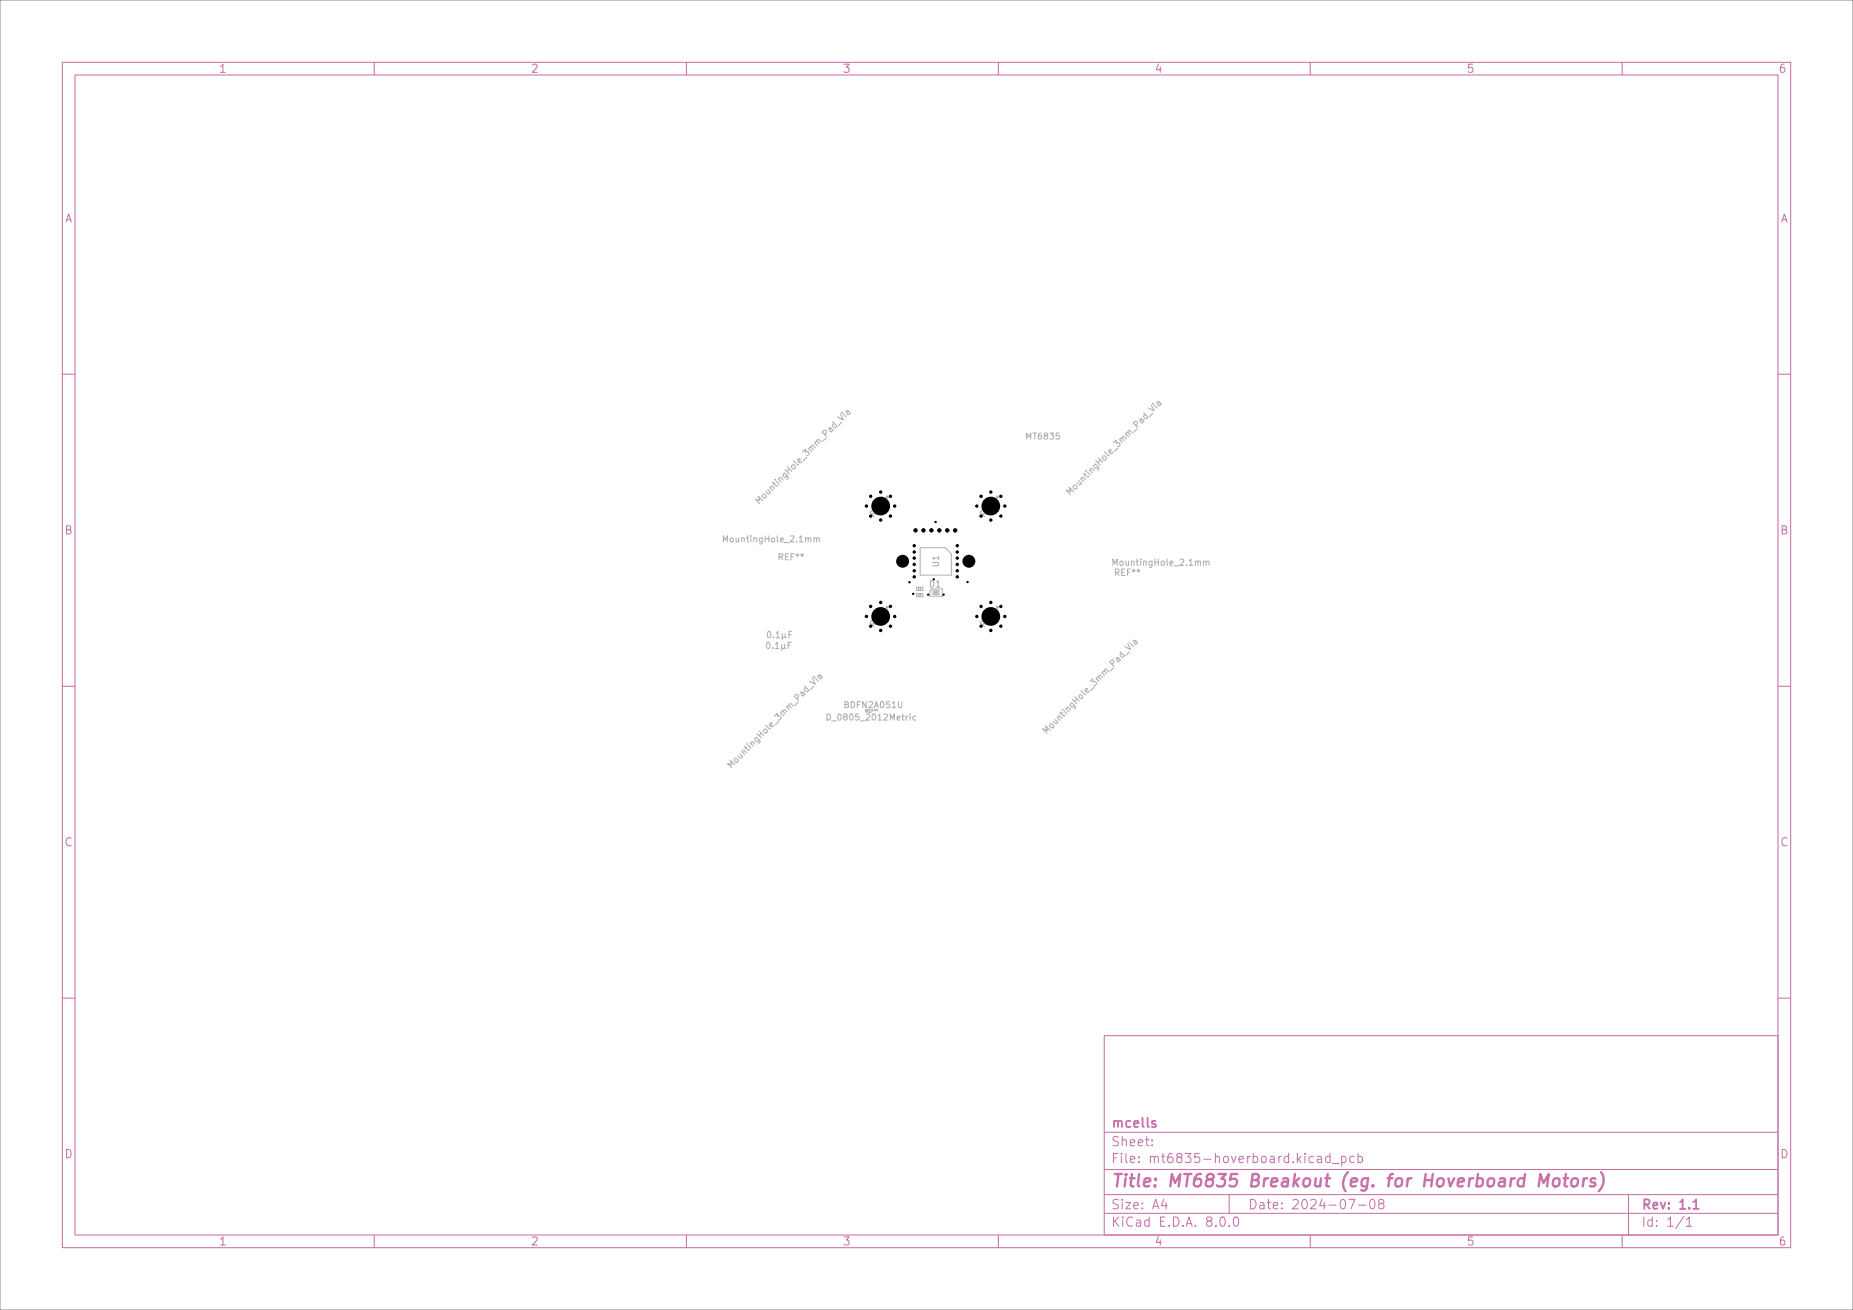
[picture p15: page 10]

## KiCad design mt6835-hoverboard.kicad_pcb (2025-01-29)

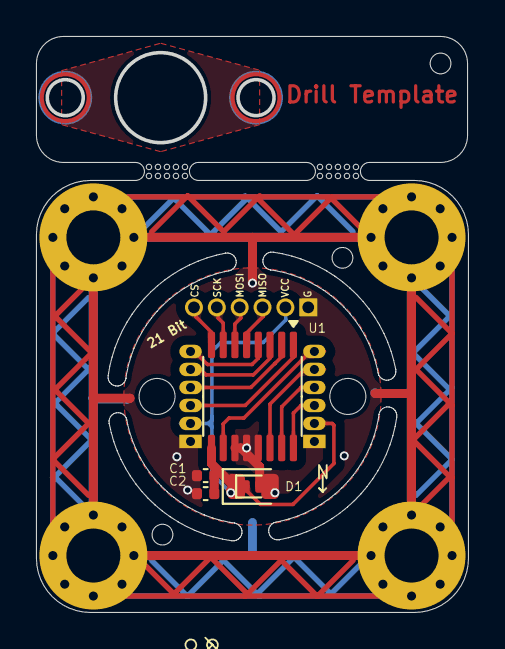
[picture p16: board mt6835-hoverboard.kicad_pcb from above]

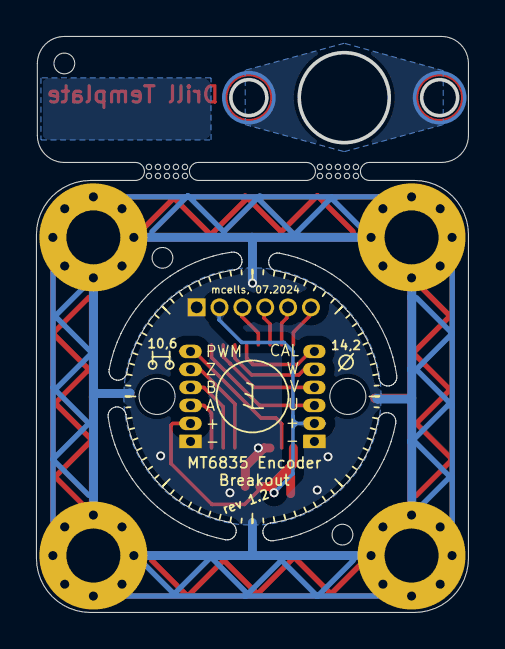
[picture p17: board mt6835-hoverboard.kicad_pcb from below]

Board: 2 copper layers, 24.0 x 32.0 mm, 7 parts (3 on the bottom side), 2 nets.

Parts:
C1, C2: 0.1µF; C_0402_1005Metric
D1: BDFN2A051U; D_SOD-882D
J1: PinHeader_1x06_P1.27mm_Vertical
J2, J3: PinHeader_1x06_P1.00mm_Vertical
U1: MT6835; TSSOP-16_4.4x5mm_P0.65mm

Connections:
GND: C1.1, C2.1, D1.2 (A2), J1.1, J2.1, J3.1, U1.11 (TEST), U1.12 (GND), U1.13 (TEST_EN)
unnamed: C1.2, C2.2, D1.1 (A1), J1.2, J2.2, J3.2, U1.9 (VDD)

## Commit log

2024-07-01 Add project files
    [mt6835-hoverboard.kicad_pcb, mt6835-hoverboard.kicad_sch]
2024-07-01 update schematic
    [mt6835-hoverboard.kicad_pcb, mt6835-hoverboard.kicad_sch]
2024-07-05 Make DRC happy, Add 25x25mm mounting and drill guide
2024-07-06 Add finishing touches to PCB
2024-07-08 Revision 1.1: Good for production
    [mt6835-hoverboard.kicad_pcb, mt6835-hoverboard.kicad_sch]
2024-07-21 Add step by step instructions for modifying a motor
2024-07-21 add isolator stls
    [Isolator-top.stl, isolator-bottom.stl]
2025-01-29 Rev 1.2: Move pinout silkscreen slightly
    [mt6835-hoverboard.kicad_pcb]
